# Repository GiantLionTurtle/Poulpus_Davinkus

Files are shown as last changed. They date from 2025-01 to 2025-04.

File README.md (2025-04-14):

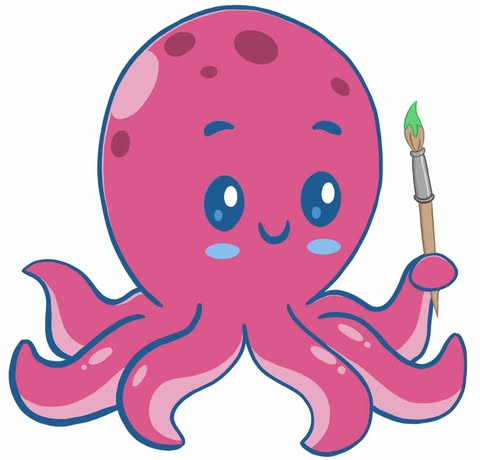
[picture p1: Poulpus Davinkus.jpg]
logo de poulpus davinkus


# Poulpus_Davinkus

Poulpus Davinkus est un projet de robot delta convergent ayant la capacité de reproduire des dessins et images à l'aide d'une sélection d'étampes et de couleurs.

https://github.com/user-attachments/assets/7dc46223-dcc0-4c87-9199-7f3be7e44d6c

## Logiciel de contrôle

Un logiciel de contôle en python permet de

* Dessiner avec les étampes disponnibles
UI avec dessin

* Analyser une image pour générer un chemin d'étampes

UI avec image analysée

Et de générer les chemins appropriés pour le robot.

L'interface est intuitif et permet de voir le statut du robot. Il peut être lancé à partir de 

```
UI/Paint.py
```

Les dépendences de l'interface sont:

* pyqt6 (interface)
* opencv-python (analyse d'image)
* matplotlib (affichage des résultats de l'analyse d'image)
* paramiko (connexion ssh avec le robot)

## Électronique de bord

Toute l'électronique de bord est alimentée par une alimentation d'ordinateur qui fournit 12v pour les moteurs (pas à pas et ventilateurs) et 5v pour les contrôleurs (Raspberry Pi 5 et Arduino Uno).

Le Raspberry Pi 5 est alimenté par un fil usb-c modifié et alimente la carte Arduino avec un cable usb qui sert également à la communication série entre les deux contrôleurs. Le chapeau "CNC Shield V3" est placé sur la carte Arduino et alimentée à 12v pour contrôler les moteurs. Les pilotes de moteurs sur le chapeau sont du modèle DRV2285 configurés pour ne laisser passer que 1A et avoir 16 niveaux de micro-pas.

## Microcode

Le microcode de l'imprimante à étampe est une version modifiée de Klipper qui supporte notre model cinématique de delta convergent. Elle peut être trouvée comme sous-module dans kinematics/ ou à https://github.com/GiantLionTurtle/klipper_convergentDelta

Dans kinematics/ se trouve aussi le fichier konfig.cfg qui est le fichier de configuration à donner à Klipper pour que le robot fonctionne comme prévu.

La cinématique du robot a l'enveloppe de travail suivante qui peut être approximée à un cylindre de 130mm de hauteur et 170mm de rayon:

Enveloppe de travail théorique

Klipper est lancé au démarrage en utilisant l'utilitaire crontab et écoute le port série virtuel à /tmp/printer/. L'interface utilisateurice pousse des lignes de gcode dans le port série en utilisant la commande

```
echo 'G28' >> /tmp/printer/
```

via une connexion SSH et en modifiant la commande entre simple guillemets.

## Mécanique

La forme du robot est inspirée par le robot de Jakub Kaminski: https://jakub-kaminski.com/delta-robot/

L'assemblage mécanique du robot consiste en 3 actuateurs linéaires identiques qui fonctionnent sur un principe de double bobinne enroulant un fil de pêche

Schema d'un actuateur linéaire

Les 3 actuateurs se rassemblent à la pointe de la pyramide inversée.

La boite de succion a 3 ventilateurs qui permettent un maintien de la feuille en place.

Les pièces à fabriquer sont les suivantes

* Barre en L en acier doux avec des trous de 3.2 mm troués avec les guides imprimés x3
* Tiges en aluminum 3/16" de 350mm x6
* Joints sphériques liés avec du JB-weld x12
    * Bille d'acier 1/2"
    * Vis M3x10
* Pièces imprimées

Quincaillerie
* Écrous M3 (6x tensionneurs; 12x assemblage chariots 6x fixation de la pointe; 9x fixation de cornerlink au plafond) x35
* Vis M3x40 (6x tensionneurs; 9x fixation de cornerlink au plafond) x15
* Vis M3x10 (12x joints sphériques; 6x fixation des poulies de fin de course) x18
* Vis M3x16 (6x fixation des barres en L à la pointe; 6x fixation des barres en L aux cornerlinks) x12
* Vis M3x18 (12x fixation des ventilateur à la boite de succion) x12
* Écrous M2 (6x fixation des interrupteurs de fin de course) x6
* Vis M2x10 (6x fixation des interupteurs de fin de course) x6
* Vis UNC 4-40 (12x fixation des moteurs par à pas) x12

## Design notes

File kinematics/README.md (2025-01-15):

# Kinematics

Code to interpret gcode and generate motor commands

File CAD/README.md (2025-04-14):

# CAD
Toutes les pièces et assemblages du robot

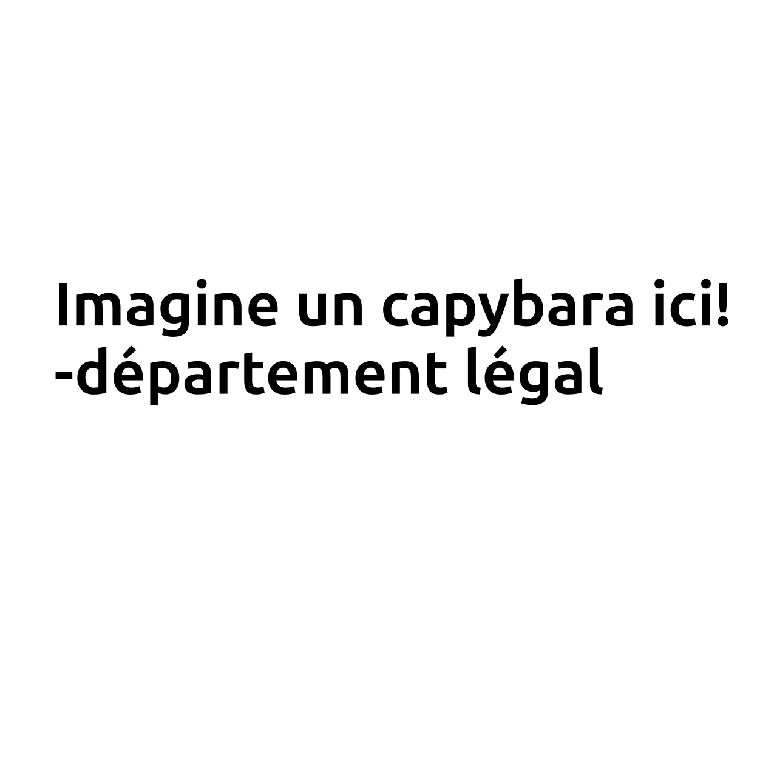
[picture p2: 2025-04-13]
UI/Images/capybara.png

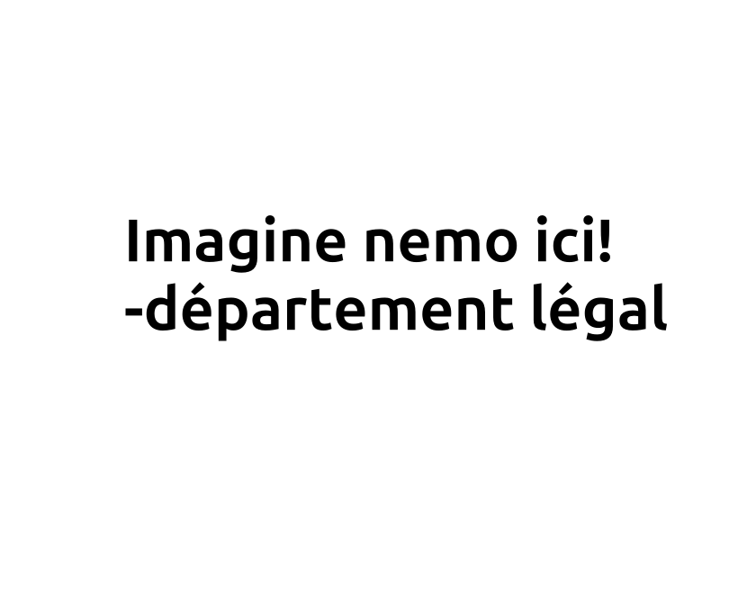
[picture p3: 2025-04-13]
UI/Images/nemo.png

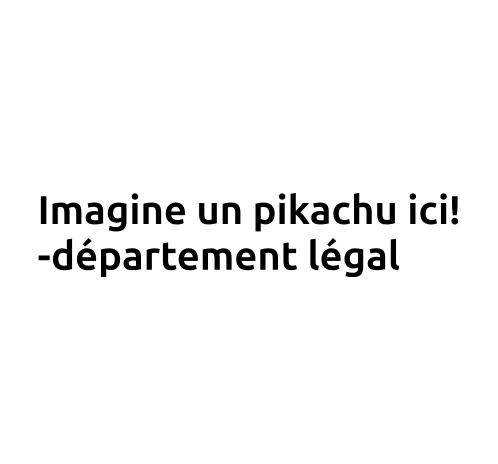
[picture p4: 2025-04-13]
UI/Images/fat_pikachu.png

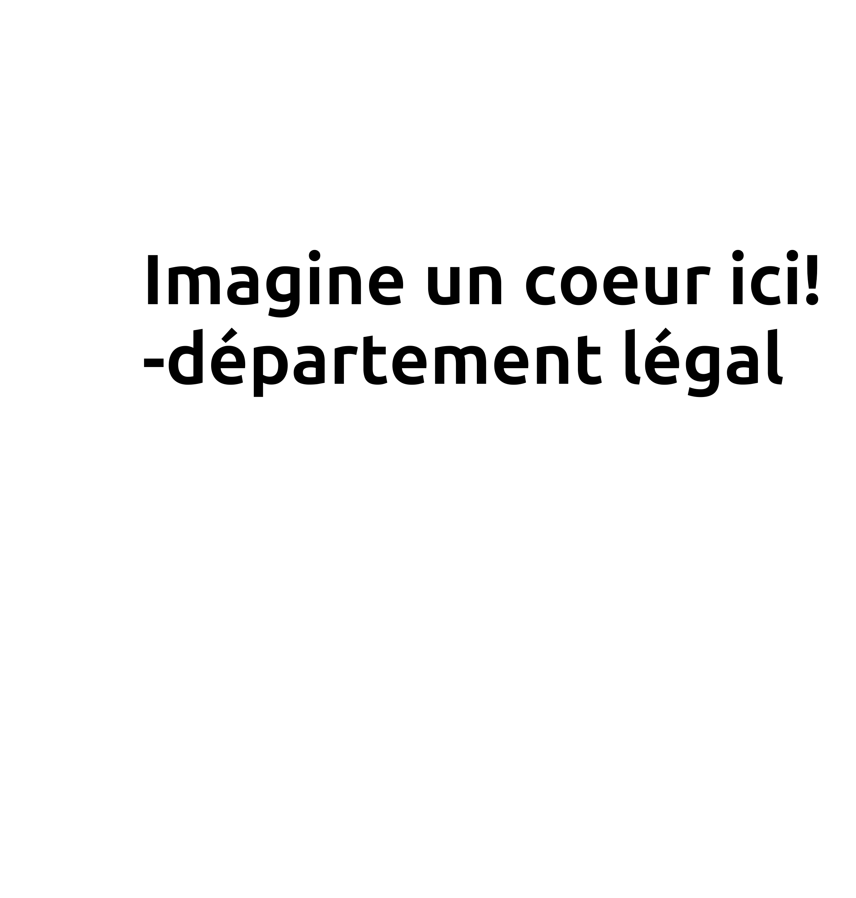
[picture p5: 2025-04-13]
UI/Images/heart.png

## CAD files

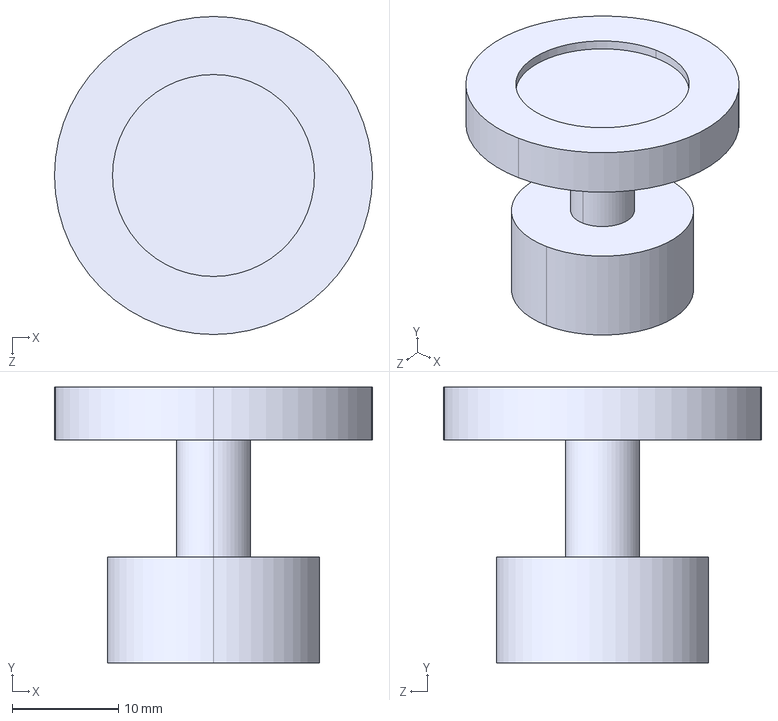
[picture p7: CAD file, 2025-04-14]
CAD/Etampe.STEP
30.0 x 26.0 x 30.0 mm

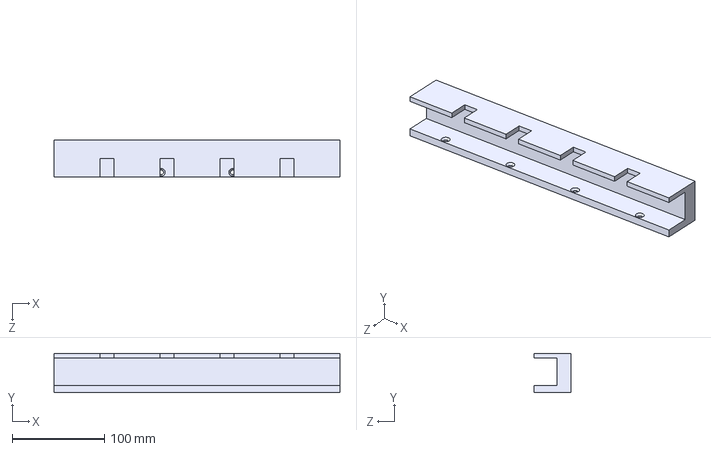
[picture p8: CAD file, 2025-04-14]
CAD/SupportEtampe.STEP
310.0 x 42.5 x 40.0 mm

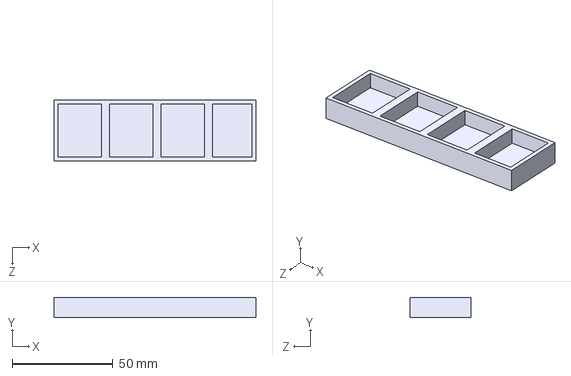
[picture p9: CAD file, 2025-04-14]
CAD/Encrier.STEP
100.0 x 10.0 x 30.0 mm

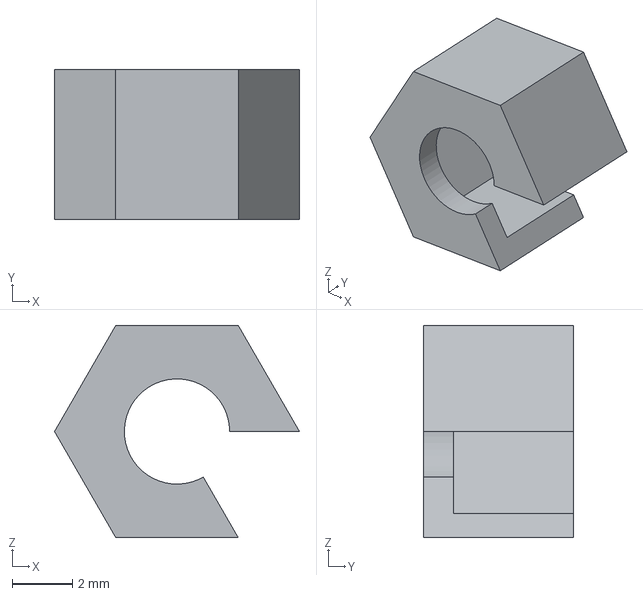
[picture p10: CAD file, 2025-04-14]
CAD/TensionerCarriage.step
8.15 x 5.00 x 7.06 mm

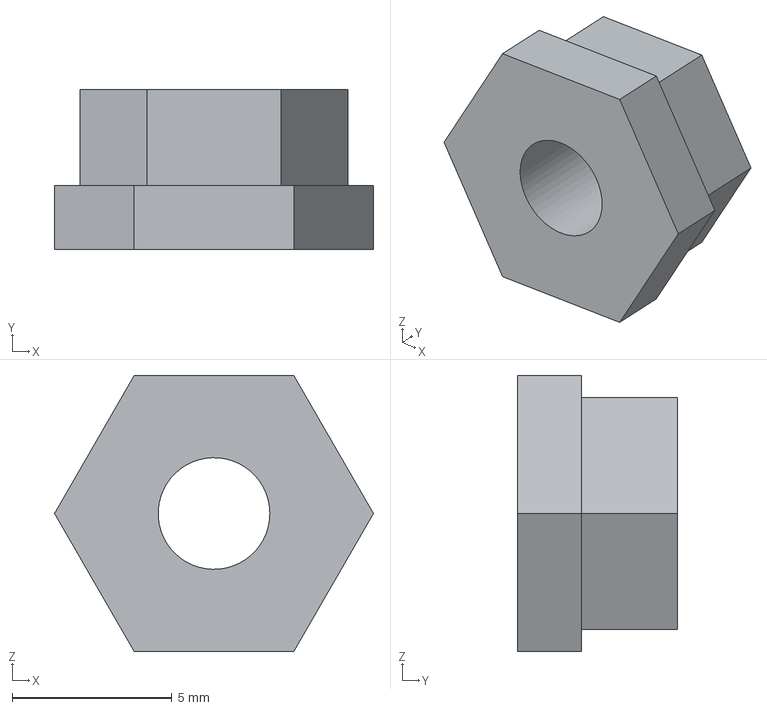
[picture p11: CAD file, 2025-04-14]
CAD/TensionerStop.step
10.0 x 5.00 x 8.66 mm

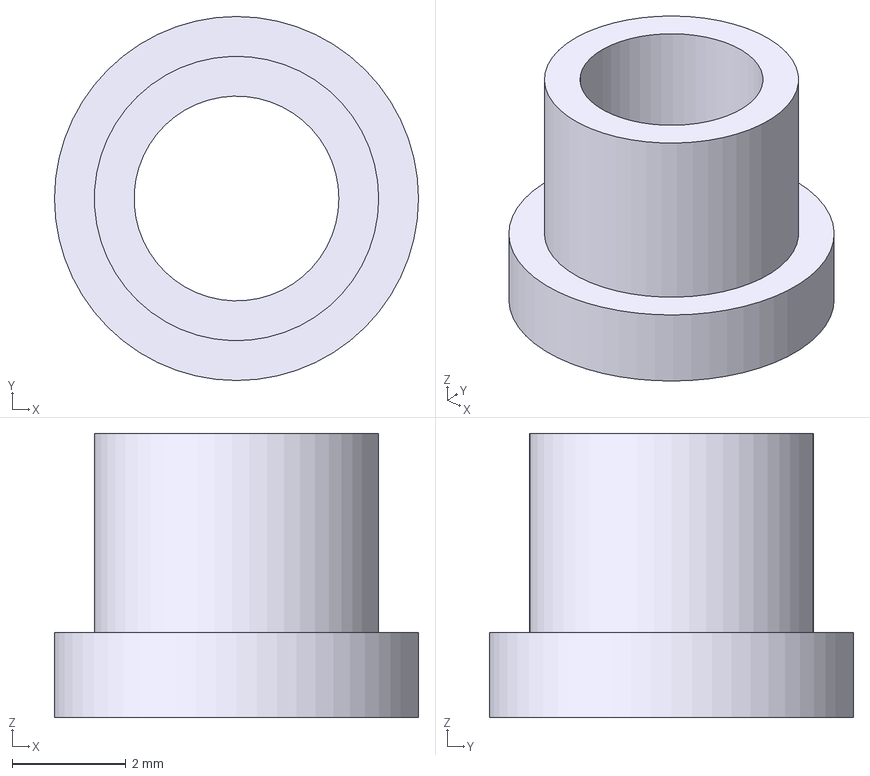
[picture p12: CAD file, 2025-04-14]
CAD/TensionerSlider.step
6.40 x 6.40 x 5.00 mm

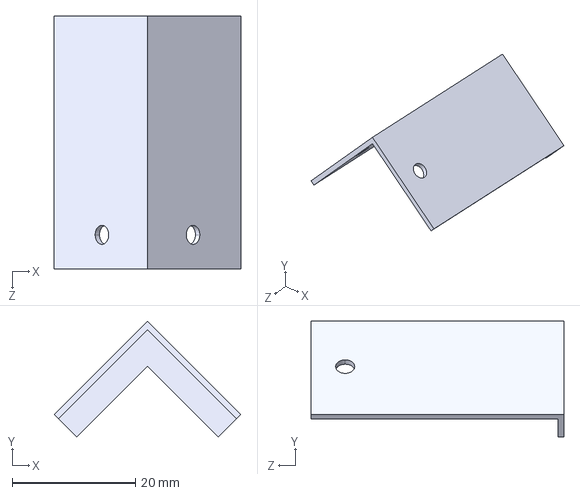
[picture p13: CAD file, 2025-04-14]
CAD/CornerLinkGuide.STEP
30.3 x 18.8 x 41.0 mm

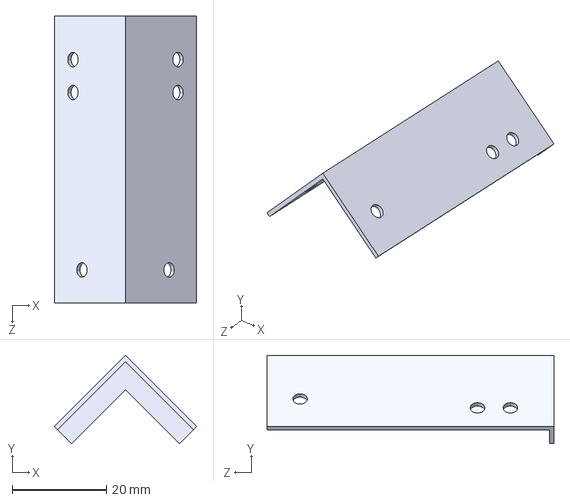
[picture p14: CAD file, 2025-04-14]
CAD/PointePyramideGuide.STEP
30.3 x 18.8 x 61.0 mm

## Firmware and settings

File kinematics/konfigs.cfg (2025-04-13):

# Arduino aliases for atmega168/328/328p boards
[board_pins arduino-standard]
aliases:
    ar0=PD0, ar1=PD1, ar2=PD2, ar3=PD3, ar4=PD4,
    ar5=PD5, ar6=PD6, ar7=PD7, ar8=PB0, ar9=PB1,
    ar10=PB2, ar11=PB3, ar12=PB4, ar13=PB5, ar14=PC0,
    ar15=PC1, ar16=PC2, ar17=PC3, ar18=PC4, ar19=PC5,
    analog0=PC0, analog1=PC1, analog2=PC2, analog3=PC3, analog4=PC4,
    analog5=PC5, analog6=PE2, analog7=PE3


[stepper_a]
step_pin: ar2
dir_pin: ar5
microsteps: 16
rotation_distance: 40
endstop_pin: ^ar9
homing_speed: 50
min_x:-199.62126191539352
min_y:-115.25138930282525
min_z:296.36011287004123
max_x:-80.2775517853331
max_y:-46.34826613314619
max_z:117.35043313649936
position_endstop:0
position_max:225.9093335133568
arm_length:300

[stepper_b]
step_pin: ar3
dir_pin: ar6
microsteps: 16
rotation_distance: 40
endstop_pin: ^ar10
min_x:199.62126191539352
min_y:-115.25138930282525
min_z:296.36011287004123
max_x:80.2775517853331
max_y:-46.34826613314619
max_z:117.35043313649936
position_endstop:0
position_max:225.9093335133568


[stepper_c]
step_pin: ar4
dir_pin: ar7
microsteps: 16
rotation_distance: 40
endstop_pin: ^ar11
min_x:0.0
min_y:230.5027786056505
min_z:296.36011287004123
max_x:0.0
max_y:92.69653226629238
max_z:117.35043313649936
position_endstop:0
position_max:225.9093335133568

[mcu]
serial: /dev/ttyACM0

[printer]
kinematics: convergent_delta
max_velocity: 300
max_accel: 3000
max_z_velocity: 150
work_radius:175
work_height:100

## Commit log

2025-01-15 Add basic kinematics functions
2025-02-05 Add the drawing prototype to the UI
2025-02-08 Remove rust implementation, add klipper_convergentDelta as submodule start dimensionner helper
    [arduino_zero.cfg, mesh.stl, positions.csv]
2025-02-09 cleanup prints
2025-02-09 modifs pour analyse d'image et setup de tests dans main ui
2025-02-17 Build stl of work enveloppe
2025-02-17 Config file for klipper
    [konfigs.cfg]
2025-02-24 Bug fixes pour l'analyse et changement du output pour seulement les cercles et conversion gcode en mm
2025-02-25 bug fix pour le draw des cercles
2025-03-05 ajout dune dataclass pour transmettre les infos pour gcode
2025-03-05 creation de deux fichiers separes pour garder un version safe et une en developpement
2025-03-06 Début de la deuxième itération de l'algo de vision et bug fixes pour le premier
2025-03-06 Remove enable pins from konfigs
    [kconfig.cfg, konfigs.cfg]
2025-03-10 Classe de communication entre ordinateur et RPI
2025-03-11 Début implémentation de la transformation de Hough
2025-03-12 Fonctions de transformation en gcode logique
2025-03-19 Ajout de l'arrière plan et fonction undo
2025-03-24 modifs pour l'isolation des shapes a laide de hsv
2025-03-25 Sélection dans la banque d'image
2025-03-25 Ajout de l'analyse préliminaire dans le mode image
2025-03-26 laisse tomber les sliders pour des images statiques
2025-03-26 Ajout d'une banque de dessins
2025-03-26 application masques sur les images
2025-03-31 more contour shenanigans (contour filtering pour les images)
2025-04-02 Changement banque de dessin et réparation du mode dessin
2025-04-02 Rotation de matrice
2025-04-02 Ajout de la communication
2025-04-02 Correction des positions
2025-04-05 contour filtering for all images except poulpus and nemo and reassemble to have one form to put stamps in
2025-04-09 Utilisation du UI quand il n'est pas branché
2025-04-09 Séquence de manipulation d'étampe
2025-04-09 Fermeture de la connection ssh quand la fenetre + chemins relatifs pour acces fichiers
2025-04-10 ca marche ish avec le coeur de teste seulement pour linstant
2025-04-10 Ajustement de la banque de dessins pour bien les télécharger
2025-04-10 Ajout du status de connection SSH dans l'interface et le progrèes du dessin par le robot
2025-04-10 modifs pour que l'analyse utilise le bon format pour la liste quil envoie a la comm
2025-04-10 enelver nemo de l'analyse et rajoter pikachu dans le UI
2025-04-10 ajustements de compatibilite entre analyse et ui
2025-04-10 Ajustement de la pregression et taille des étampes
2025-04-10 Ajustement pour avoir la bonne taille des étampes
2025-04-10 ajustements des positions d'encrage
2025-04-10 Ajustement du progrès des étampes pour le mode image
2025-04-10 Fixer les couleurs pour chaque étampe
2025-04-10 Changement index pool pour les couleurs
2025-04-11 ligne pour envoyer les commandes en ssh de l'analyse
2025-04-11 Petites modifs de clean up
2025-04-13 Changement de LICENSE
2025-04-13 Vieux fichiers retirés
    [arduino_zero.cfg]
2025-04-13 Retrait de fichiers innutilises
2025-04-13 Ajustement de l'interface pour la remise
2025-04-13 Retirer les fichiers qui ne sont pas utilisés
2025-04-13 Ajustement des commentaires pour l'interface
